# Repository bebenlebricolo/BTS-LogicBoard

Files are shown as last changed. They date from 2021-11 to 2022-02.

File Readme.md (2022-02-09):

# Index
- [BTS-LogicBoard](#bts-logicboard)
- [Features](#features)

# BTS-LogicBoard
Beer thermoregulation system logic board.
This board is meant to provide a PWM control signal to the [BTS-MainBoard-Control](https://github.com/bebenlebricolo/BTS-MainBoard-Control) board and will be driven by different input sources :
  1. External input mechanisms, implying and external trigger signal and a mechanical user interface such as switches and potentiometers.
  2. Temperature sensor(s) using thermistor based sensors

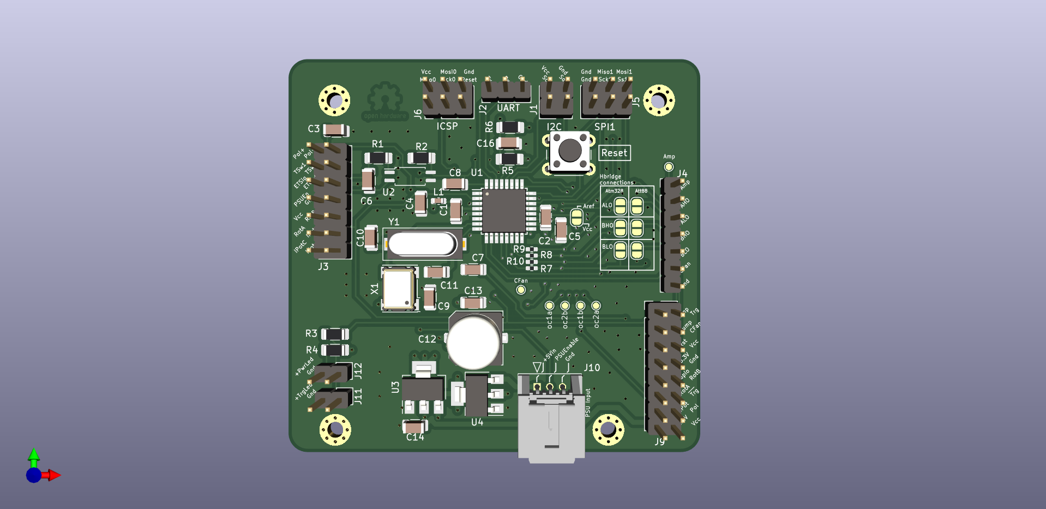
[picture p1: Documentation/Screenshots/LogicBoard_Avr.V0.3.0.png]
Screenshot V0.3.0

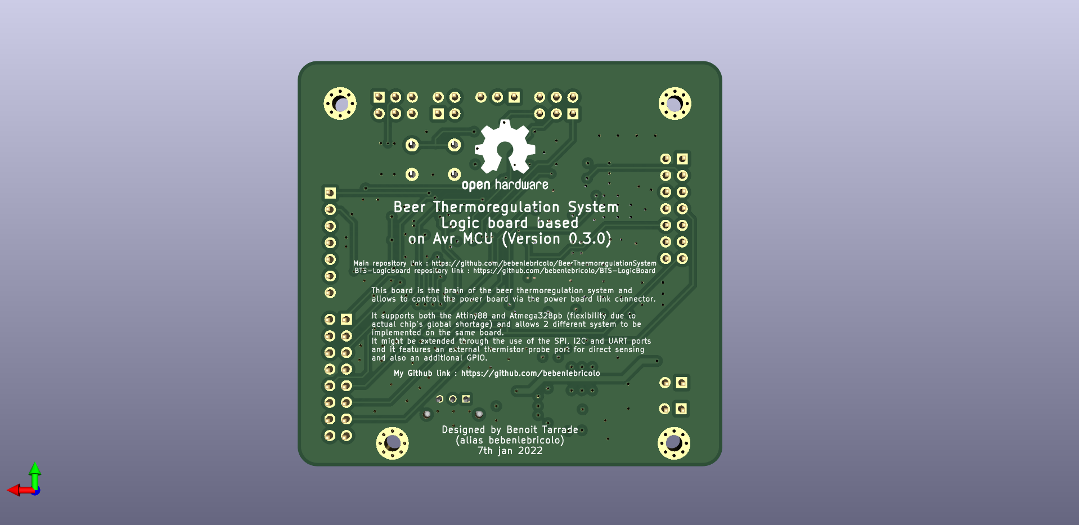
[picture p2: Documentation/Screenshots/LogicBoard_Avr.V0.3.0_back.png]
Screenshot V0.3.0


For more details on the current implementation, see [Notes of version 0.3.0](Notes/Notes_v0.3.0.md).

## 1. External triggering signal specificities
The later option was the first the be developped as it allowed to use an external regulation device as the triggering signal source (using a different power supply).
The input triggering signal is either *ON* or *OFF*.
As a consequence, we also need to get the "polarity" information, tells the system to warm up or cool down the thermal fluid.

## 2. Automatic temperature regulation using temperature sensors

This board is envisioned as a starting point as it only embeds generic electronic devices, meaning no code at all.
I've done this on purpose, to keep things relatively simple and eliminating the need to iterate over software revisions, bug fixes, etc.
As the functionalities implemented by this board are relatively simple, I thought it would be a nice alternative to go only with a NE555 (the famous one) and few other electronic components such as comparators and logic gates to perform the basic functions.

# Features
This boards boats the following features :
* 1 MHz (or so) PWM signal with linear (...or so) duty cycle control
* Cooling fan automatic turn on when board is enabled and turn off after a precalculated delay (around 120s) when the board is disabled
* Externaly driven : the PWM signal only starts up when an input signal is applied on the enable pins. This is meant to receive a pump driver signal in order to start up
* Mechanical interface (switches and potentiometer) with status leds
  * Power on status LED
  * PWM enabled status LED
  * PWM intensity status LED

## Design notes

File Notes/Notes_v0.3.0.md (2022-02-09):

- [Notes on board prototype version v0.3.0](#notes-on-board-prototype-version-v030)
- [Improvements from v0.2.0](#improvements-from-v020)
- [High speed PWM (1MHz +) using hardware timers and PWM](#high-speed-pwm-1mhz--using-hardware-timers-and-pwm)
- [Small issues](#small-issues)
  - [Hand soldering is quite challenging](#hand-soldering-is-quite-challenging)

# Notes on board prototype version v0.3.0
This board is built around 2 chips : either an Attiny88 or an Atmega328PB and accepts both. This choice of dual compatibility was made during the global chip shortage (2021/2022) and thus I had to find solutions to build the board with components I had at hands (Attiny88) in case the Atmega328PB were out of stock until late 2023.
As a result, as the Attiny88 is not as powerful and full featured as the Atmega328PB, some functionalities such as the UART and automatic HBridge free-wheeling won't be available ; and probably user interface will be leaner.

# Improvements from v0.2.0
* Switched to plain MCU design, noise sensitivity is reduced
* All important tracks were adjusted to be 50Ohms Z0 (characteristic impedance) in order to reduce signal reflection to a minimum
* Drive termination resistors were added on HBridge drive side (around 33 Ohms) to adapt for the ~20ish Ohms of Atmel chip's output characteristic impedance
* Tracks were optimized, as short and straight as possible, minimizing capacitive cross talk whenever possible (orthogonal track crossing as much as possible)
* Switching to 4 layers stackup design : signal (top), gnd, power, signal (bottom)
* Supports external triggering via the optocoupler
* Supports external triggering via signals headers for other extensions
* Provides Uart, Spi and I2C serial interfaces
  * The board could be extended with I2C screen, UART log channel, I2C/SPI additional temperature probes, etc..
* Extension friendly : user interface could be extended either using potentiometers, rotary encoders, switches in various configurations.

# High speed PWM (1MHz +) using hardware timers and PWM
Using hardware timers and PWM generation we can achieve 1MHz PWM with 1/12th (Attiny88) or 1/20th (Atmega328PB) resolution
We can also speed it up even more, sacrificing intermediate steps
This is required in order to take advantage of the high current inductors (10µH / 12A DC) which need to be run at very high frequencies in order to get the proper smoothing effect from them.

# Small issues
## Hand soldering is quite challenging
Hand soldering is quite challenging indeed because of the following points :
* Zones use direct and solid connection with all the pads ! -> soldering iron has to push a lot of heat before the solder starts to melt
  * Switch to thermal relief connection for all pads that don't require strong and stable GND/Power connections

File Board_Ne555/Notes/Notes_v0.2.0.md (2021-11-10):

- [Notes on board prototype version v0.2.0](#notes-on-board-prototype-version-v020)
- [Improvements from v0.1.0](#improvements-from-v010)
- [Fine(r) control over PWM duty cyle](#finer-control-over-pwm-duty-cyle)
- [Small issues](#small-issues)
  - [PWM controller speed is lower than the previous iteration, but this is an easyfix](#pwm-controller-speed-is-lower-than-the-previous-iteration-but-this-is-an-easyfix)
  - [Potentiometer wiring is reversed](#potentiometer-wiring-is-reversed)
  - [Output PWM goes up into the switch and goes down again on the board](#output-pwm-goes-up-into-the-switch-and-goes-down-again-on-the-board)
  - [When board is disabled (no input signal), output is still driven by the comparator](#when-board-is-disabled-no-input-signal-output-is-still-driven-by-the-comparator)

# Notes on board prototype version v0.2.0
This board prototype was called 'board-v1.1' earlier and I decided to rename it as v0.2.0 as semantically speaking, this board is also still a prototype (as the v0.1.0 was).
This board is built around a NE555 and fixes some important aspects of the first iteration.

# Improvements from v0.1.0
* Switched the NE555 PWM implementation to a fixed duty-cycle one and derive the PWM using a comparator
* Added hysteresis network resistors in comparators input circuitry
* Used CMOS NOT gates to handle input signal without impacting the other circuits
* Used an optoisolator to fully isolate the "external" circuitry from this one
* Remapped switches in order to have a more natural pin mapping
* Used a SPDT switch to enable / disable the circuit (PWM disable function is provided by the optoisolator circuitry).
* Added a status LED to indicate the PWM intensity
* Fine(r) control over PWM duty cycle
* Updated output connector wiring with a new inhibit pin (unused by this board, left for later use)

# Fine(r) control over PWM duty cyle
The PWM duty cycle control is done using the "pseudo sawtooth" signal taken from the NE555 load capacitor's charging/discharging cycles and comparing this signal with a constant voltage level, provided by the "Power control" potentiometer.
As its name states, the potentiometer effectively controls the output power of the system by varying the On time of the PWM ; the higher the duty cycle gets, the more power is requested.

However, the PWM control is far from perfect as the pseudo sawtooth signal is not a clean triangle wave and as such, the response is not really linear.
It is quite linear in the middle of the waveform, however the top and bottom edges are quite round and asymetrical.
As a result, it is really difficult to get a small duty cycle out the PWM controller and the generated PWM jumps almost directly from 0% to around 25/30%.
The same holds true for the high power side, although it is not as marked as the lower one.

# Small issues
## PWM controller speed is lower than the previous iteration, but this is an easyfix
The output PWM frequency is around 250kHz and is lower than the previous iteration (was between 400kHz - 750kHz).
This is mostly due to the fact that the NE555 circuit uses fairly high values for the resistors and capacitors to generate the signal and as such, this is an easy fix as we simply need to update those values to lower ones.

## Potentiometer wiring is reversed
The logic of the PWM comparator is reversed, this means that turning the knob to the right (the usual "more power" direction) actually decreases the duty cycle and vice-versa. This is an easy fix as well as we simply need to reverse the potentiometer wiring (connecting the + side to the left and - side to the right with the middle pin unchanged).

## Output PWM goes up into the switch and goes down again on the board
This has not shown to be an issue in itself while testing the board, however mechanically rerouting the PWM signal within the switch makes it go back and forth in non-isolated wires. If the wire length increases, it can easily pick up some ambient noise (acting as an antenna) and we might also observe signal reflection because we are expecting to be working around 1MHz.
A solution may consist in switching the signal using mosfet as unidirectional switches, without the signal leaving the board and making a loop.

## When board is disabled (no input signal), output is still driven by the comparator
I forgot to add an output protection layer that prevents the board from outputing a 100% duty cycle even when the NE555 is disabled.
This is due to the fact that the output stage is directly driven by the output comparator, and in some configurations lowering the potentiometer level low enough eratically triggers the comparator, which in turns generate a weird looking "PWM" signal (aperiodic). This stray output signal might cause some issues as it will trigger the power boards anyway, but without any cooling (fans are turned off in such a configuration).

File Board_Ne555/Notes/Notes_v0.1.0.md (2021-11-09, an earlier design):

- [Notes on board prototype version v0.1.0](#notes-on-board-prototype-version-v010)
- [Design flaws](#design-flaws)
  - [Comparators are messed up](#comparators-are-messed-up)
  - [PWM generator (NE555)](#pwm-generator-ne555)
  - [Switches are not mapped correctly](#switches-are-not-mapped-correctly)
  - [Input transistor network for the reset ability](#input-transistor-network-for-the-reset-ability)
  - [Input "pump on" signal is not isolated](#input-pump-on-signal-is-not-isolated)
  - [Fan triggering system does not really perform as expected](#fan-triggering-system-does-not-really-perform-as-expected)
  - [Enable/Disable switch implements the same feature twice](#enabledisable-switch-implements-the-same-feature-twice)
- [Proposed improvements](#proposed-improvements)
- [Bottomline](#bottomline)

# Notes on board prototype version v0.1.0
This board prototype was called 'board-v1' earlier and I decided to rename it as v0.1.0 as semantically speaking, this board was not ready yet.
This board was built around a NE555 and has several design flaws. It is **not** viable and burns as soon as we try to connect everything together.

# Design flaws
As said above, this board embeds quite a few errors :
## Comparators are messed up
* Both comparators had flipped 4 and 5 pins, as a result, there is some current rejection from Vdd through the input pins
* Both comparator are **not** 12V compatible : using 12V on VDD creates some magic smoke out of them (you learn the hard way... don't you ?)
* Both comparators [ONSemi's NCS2252](https://www.onsemi.com/pdf/datasheet/ncs2250-d.pdf) are in fact open drain and required extra output pullup resistor
* Comparators do not embed hysteresis resistor network, switch is quite sensitive and produces a fair amount of noise.

## PWM generator (NE555)
PWM generation is not stable, frequency varies with the potentiometer's input, which is not part of the "requirement".
Output signal is quite awful, we don't end up with a clean square wave

## Switches are not mapped correctly
Output pins on the board do not follow a natural pattern and is mapped like so :

| footprint | switch |
| --- | --- |
| 1 - 2 | 1 - 6  |
| 3 - 4 | 2 - 5  |
| 5 - 6 | 3 - 4  |

So it's really easy to mess up the wiring and end with something that really does not behave as expected.

## Input transistor network for the reset ability
Input transistor network fails to trigger the reset pin of the NE555 as the transistor in charge of this action saturates at 0.7V, which is still above the NE555's input threshold value for this pin. Next design implements a harder pull-down action using a saturated NPN with the collector-emitter voltage of 0.2V, which is plenty enough to turn off the NE555.

## Input "pump on" signal is not isolated
In the system that I'm using, the pump is driven by another system, on its own SMPS (Switching mode power supply).
As such, we don't really know about the ground connection of the other system and we can end with a floating gnd which is then connected to our system, potentially triggering some faults in the ATX power supply or worse, burning things down.
A solution would be to implement an optoisolated interface for the pump signal (aka start up signal). This is done in the next revision of this board.

## Fan triggering system does not really perform as expected
The fan triggering system was meant to provide a startup signal for the cooling fan driver, located on the BTS-MainBoard-Control board.
The main purpose of the input circuitry was to charge up a capacitor, then leaving it to discharge slowly for a preestablished time (around 120 seconds).
As I remember it, the overall system was not performing well and this was mostly due to the fact that input transistor network had some cross interferences between each transistors. I remedied this in the next revision with proper NOT gates and high speed comparators.

## Enable/Disable switch implements the same feature twice
The enable/Disable switch is used to turn the ATX power supply and enable the PWM signal at the same time.
We could simply rely on the pump activation in order to provide the same kind of functionality.

# Proposed improvements
* Switch the NE555 PWM implementation to a fixed duty-cycle one and derive the PWM using a comparator
* Add hysteresis network resistors in comparators input circuitry
* Use CMOS NOT gates to handle input signal without impacting the other circuits
* Use an optoisolator to fully isolate the "external" circuitry from this one
* Remap switches in order to have a more natural pin mapping
* Use a SPDT switch to enable / disable the circuit (PWM disable function is provided by the optoisolator circuitry).

# Bottomline
This board did provide some value as it clearly pointed out the design flaws of this iteration and gave me some good ideas on how to implement a new system.
However, I tried to fix this board with tiny wires, remapping pins and adding resistors ; however this whole new "flying" network made up for great antennas and completely defeated the purpose of having a "clean" PWM generation.

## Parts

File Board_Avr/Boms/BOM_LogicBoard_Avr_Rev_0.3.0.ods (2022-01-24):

Logic Board Avr revision 0.3.0 BOM sheet
Reference | Quantity | Value | Footprint | Datasheet
C1 C2 C6 C8 C9 C16 | 6 | 100nF | Capacitor_SMD:C_1206_3216Metric
C10 C11 | 2 | 10pF | Capacitor_SMD:C_1206_3216Metric
C12 | 1 | 470uF | Capacitor_SMD:C_Elec_8x6.2
C3 C4 C7 | 3 | 330nF | Capacitor_SMD:C_1206_3216Metric
C5 C13 C14 | 3 | 1uF | Capacitor_SMD:C_1206_3216Metric
H1 H2 H3 H4 | 4 | MountingHole_Pad | MountingHole:MountingHole_2.5mm_Pad_Via
J1 | 1 | I2C_Interface | Connector_PinHeader_2.54mm:PinHeader_2x02_P2.54mm_Vertical
J10 | 1 | PSU Connector | BTS-LogicBoard:559350310
J11 | 1 | TriggeredStatusLedConnector | Connector_PinHeader_2.54mm:PinHeader_1x02_P2.54mm_Vertical
J12 | 1 | PowerStatusLedConnector | Connector_PinHeader_2.54mm:PinHeader_1x02_P2.54mm_Vertical
J2 | 1 | UART_Interface | Connector_PinHeader_2.54mm:PinHeader_1x03_P2.54mm_Vertical
J3 | 1 | Mechanical user interface main connector | Connector_PinHeader_2.54mm:PinHeader_2x07_P2.54mm_Vertical
J4 | 1 | Power board connector | Connector_PinHeader_2.54mm:PinHeader_1x07_P2.54mm_Vertical
J5 | 1 | SPI Connector | Connector_PinHeader_2.54mm:PinHeader_2x03_P2.54mm_Vertical
J6 | 1 | ICSP Header | Connector_PinHeader_2.54mm:PinHeader_2x03_P2.54mm_Vertical
J9 | 1 | GPIO Connector | Connector_PinHeader_2.54mm:PinHeader_2x08_P2.54mm_Vertical
JP1 | 1 | Aref_jumper | Jumper:SolderJumper-2_P1.3mm_Open_RoundedPad1.0x1.5mm
JP2 | 1 | HB_ALO_AT88_JP | Jumper:SolderJumper-2_P1.3mm_Open_RoundedPad1.0x1.5mm
JP3 | 1 | HB_ALO_ATM328_JP | Jumper:SolderJumper-2_P1.3mm_Open_RoundedPad1.0x1.5mm
JP4 | 1 | HB_BHO_AT88_JP | Jumper:SolderJumper-2_P1.3mm_Open_RoundedPad1.0x1.5mm
JP5 | 1 | HB_BHO_ATM328_JP | Jumper:SolderJumper-2_P1.3mm_Open_RoundedPad1.0x1.5mm
JP6 | 1 | HB_BLO_AT88_JP | Jumper:SolderJumper-2_P1.3mm_Open_RoundedPad1.0x1.5mm
JP7 | 1 | HB_BLO_ATM328_JP | Jumper:SolderJumper-2_P1.3mm_Open_RoundedPad1.0x1.5mm
L1 | 1 | BLM18AG151SN1D | Capacitor_SMD:C_0603_1608Metric | https://docs.rs-online.com/b10d/0900766b811b5866.pdf
R1 R2 R3 R4 | 4 | 1k | Resistor_SMD:R_1206_3216Metric_Pad1.30x1.75mm_HandSolder
R5 | 1 | 10k | Resistor_SMD:R_1206_3216Metric_Pad1.30x1.75mm_HandSolder
R6 | 1 | 330 | Resistor_SMD:R_1206_3216Metric_Pad1.30x1.75mm_HandSolder
R7 R8 R9 R10 | 4 | 33 | Resistor_SMD:R_0402_1005Metric_Pad0.72x0.64mm_HandSolder
SW1 | 1 | Reset switch | Button_Switch_THT:SW_PUSH_6mm_H4.3mm
TP1 TP2 TP3 TP4 TP5 TP6 | 6 | TestPoint | TestPoint:TestPoint_Pad_D1.0mm
U1 | 1 | ATmega328PB-A | Package_QFP:TQFP-32_7x7mm_P0.8mm | http://ww1.microchip.com/downloads/en/DeviceDoc/40001906C.pdf
U2 | 1 | TLP291 | Package_SO:SOIC-4_4.55x2.6mm_P1.27mm | https://toshiba.semicon-storage.com/info/docget.jsp?did=12884&prodName=TLP291
U3 | 1 | NCP603SN330T1G | Package_SO:TSOP-5_1.65x3.05mm_P0.95mm | https://www.onsemi.com/pdf/datasheet/ncp603-d.pdf
U4 | 1 | LM1117-5.0 | Package_TO_SOT_SMD:SOT-223-3_TabPin2 | http://www.ti.com/lit/ds/symlink/lm1117.pdf
X1 | 1 | ASV-12.000MHZ-EJ-T | Oscillator:Oscillator_SMD_Abracon_ASV-4Pin_7.0x5.1mm | http://www.abracon.com/Oscillators/ASV.pdf
Y1 | 1 | ABLS-20.000MHz-16-A-4-H-T | BTS-LogicBoard:Crystal_SMD_TH_Combo_HC49-SD

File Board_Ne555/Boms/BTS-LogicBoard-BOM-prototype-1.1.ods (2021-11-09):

References | Quantity | Value | Unit price (€ ) As seen on RS | Price onboard | Component | Description | RS Part code | RS link | Vendor
C4 C13 | 2 | 1uF | 0,04 | 0,08 | GRM31MF51E475ZA01L | Unpolarized capacitor | 723-6629 | link (https://fr.rs-online.com/web/p/condensateurs-ceramique-multicouches/7236629/?sra=pmpn) | Murata
C5 C8 | 3 | 470uF | 0,35 | 1,05 | NAZT471M25V10X10.5LBF | Polarized capacitor | 742-3582 | link (https://fr.rs-online.com/web/p/condensateurs-electrolytiques/7423582) | NIC Components
C3 C9 C10 C11 C12 | 5 | 100nF | 0,113 | 0,565 | C3216JB2A104K | Unpolarized capacitor | 371-6714 | link (https://fr.rs-online.com/web/p/condensateurs-ceramique-multicouches/3716714/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) | TDK
C6, | 1 | 10nF | 0,181 | 0,181 | 223860115636 | Unpolarized capacitor | 669-8442 | link (https://fr.rs-online.com/web/p/condensateurs-ceramique-multicouches/6698442/) | Yageo
C7 (470pF instead) | 1 | 220pF | 0,026 | 0,026 | 12065A100JAT2A | Unpolarized capacitor | 136-4357 | link (https://fr.rs-online.com/web/p/condensateurs-ceramique-multicouches/1364357) | AVX
D1 D3 D4 | 3 | LED | 0,091 | 0,273 | L-132XGD | Light emitting diode | 860-9797 | link (https://fr.rs-online.com/web/p/led/8609797) | Kingbright
D2 | 1 | 1N4148W | 0,061 | 0,061 | 1N4148W | 75V 0.15A Fast Switching Diode, SOD-123 | 7003671P | link (https://fr.rs-online.com/web/p/diodes-de-commutation/7003671P/) | Vishay
H1, H2, H3, H4, | 4 | MountingHole_Pad | 0 | 0 | NA | Mounting Hole with connection | NA | NA | NA
J5 | 1 | Signal out connector (x6) | 0,461 | 0,461 | 505578-0671 | Molex MicroLock Plus connector (angled), 6 pins, 2Amps | 186-5197 | link (https://fr.rs-online.com/web/p/embases-circuits-imprimes/1865197) | Molex
J2, | 1 | Power connector (x3 pins) | 0,367 | 0,367 | 55935-0310 | Molex MicroClasp connector (angled), 3 pins, 3Amps | 188-024 | link (https://fr.rs-online.com/web/p/embases-circuits-imprimes/0188024) | Molex
J1 J4 | 2 | Switches connectors (03x02, + pins) | 0,217 | 0,434 | DF11-6DP-2DSA(08) | Hirose DF11 series, 6 pins, 2 rows, 2Amps | 605-6829 | link (https://fr.rs-online.com/web/p/embases-circuits-imprimes/6056829) | Hirose
J3, replaced by 2x1 header | 1 | Input pump on signal | 0,102 | 0,102 | 640454-2 | MTA-100, 2 pins 5.0A | 766-6604 | link (https://fr.rs-online.com/web/p/embases-circuits-imprimes/5355181) | TE-Connectivity
Q1 | 1 | BC817 | 0,173 | 0,173 | BC817-25LT3G | 0.8A Ic, 45V Vce, NPN Transistor, SOT-23 | 690-0076 | link (https://fr.rs-online.com/web/p/transistors-bipolaires/6900076/) | ON Semiconductor
R2 R4 R5 R13 R20 | 5 | 1k | 0,038 | 0,19 | CRG1206F1K0 | Resistor | 125-1190 | link (https://fr.rs-online.com/web/p/resistances-cms/1251190/) | TE-Connectivity
R14 R17 R18 | 3 | 56k | 0,074 | 0,222 | CRCW120656K0FKEA | Resistor | 679-223 | link (https://fr.rs-online.com/web/p/resistances-cms/6792231/) | Vishay
R1 R9 R12 R15 | 4 | 470 | 0,194 | 0,776 | CR1206-JW-471GLF | Resistor | 740-9120 | link (https://fr.rs-online.com/web/p/resistances-cms/7409120/) | Vishay
R19 (replaced by 5.6k) | 1 | 4.7k | 0,028 | 0,028 | CRG1206F4K7 | Resistor | 125-1191 | link (https://fr.rs-online.com/web/p/resistances-cms/1251191/) | TE-Connectivity
R7 R10 R11 | 3 | 10k | 0,029 | 0,087 | CRG1206F10K | Resistor | 125-1192 | link (https://fr.rs-online.com/web/p/resistances-cms/1251192/) | TE-Connectivity
R3 | 1 | 390k | 0,064 | 0,064 | CRCW1206390KFKEA | Resistor | 679-2073 | link (https://fr.rs-online.com/web/p/resistances-cms/6792073/) | Vishay
R6 | 1 | 220 | 0,11 | 0,11 | CRG1206F220R | Resistor | 223-2164 | link (https://fr.rs-online.com/web/p/resistances-cms/2232164/) | TE Connectivity
R8 R16 | 2 | 5.6k | 0,038 | 0,076 | CRG1206F5K6 | Resistor | 223-2366 | link (https://fr.rs-online.com/web/p/resistances-cms/2232366) | TE Connectivity
RV1, | 1 | R_POT | 0,82 | 0,82 | PTV09A-4225F-B103 | Potentiometer | 827-4990 | link (https://fr.rs-online.com/web/p/potentiometres/8274990/) | Bourns
SW1, SW2, | 2 | SW_DPDT_x2 | 3,35 | 6,7 | 2-1825138-8 | Switch, dual pole double throw, separate symbols | 710-9927 | link (https://fr.rs-online.com/web/p/interrupteurs-a-levier/7109927/) | TE-Connectivity
TP1 TP2 TP3 TP4 TP5 | 5 | TestPoints | 0 | 0 | NA | test point | NA | NA | NA
U1 U6 | 2 | NCS2252SN2T1G | 0,5 | 1 | NCS2252SN2T1G | Precisiong comparator, rail to rail (5V max) | 185-9083 | link (https://fr.rs-online.com/web/p/comparateurs/1859083/) | On Semiconductor
U4 | 1 | TLP291 | 0,14 | 0,14 | TLP291(Y,SE(T | Optocoupler / Optoisolator 80V | 896-2555 | link (https://fr.rs-online.com/web/p/optocoupleurs/8962555) | Toshiba
U3 U5 | 2 | 74HC1GU04 | 0,04 | 0,08 | 74HC1GU04GW-Q100,1 | Not gate (CMOS inverter) | 152-6496 | link (https://fr.rs-online.com/web/p/inverseurs/1526496/) | Nexperia
U8 | 1 | LM1117IMP-5,0 | 1,334 | 1,334 | LM1117IMP-5.0/NOPB | 5V LDO regulator, SOT-223 | 535-8641 | link (https://fr.rs-online.com/web/p/regulateurs-de-tension/5358641/) | Texas Instruments
U2, | 1 | NE555D/TS555 | 0,359 | 0,359 | NE555DR | Precision Timers, 555 compatible, SOIC-8 | 197-7393 | link (https://fr.rs-online.com/web/p/timers/1977393/) | Texas Instruments
Total component price (€)
15,759
Optional
Description | Reference | Manufacturer | Part number | Unit price
Wire to board Connector | MTA-100 | TE-Connectivity | 3-640441-2 | 0,271 | 543-7700 | link (https://fr.rs-online.com/web/p/connecteurs-idc/5437700)
 | 2 wires

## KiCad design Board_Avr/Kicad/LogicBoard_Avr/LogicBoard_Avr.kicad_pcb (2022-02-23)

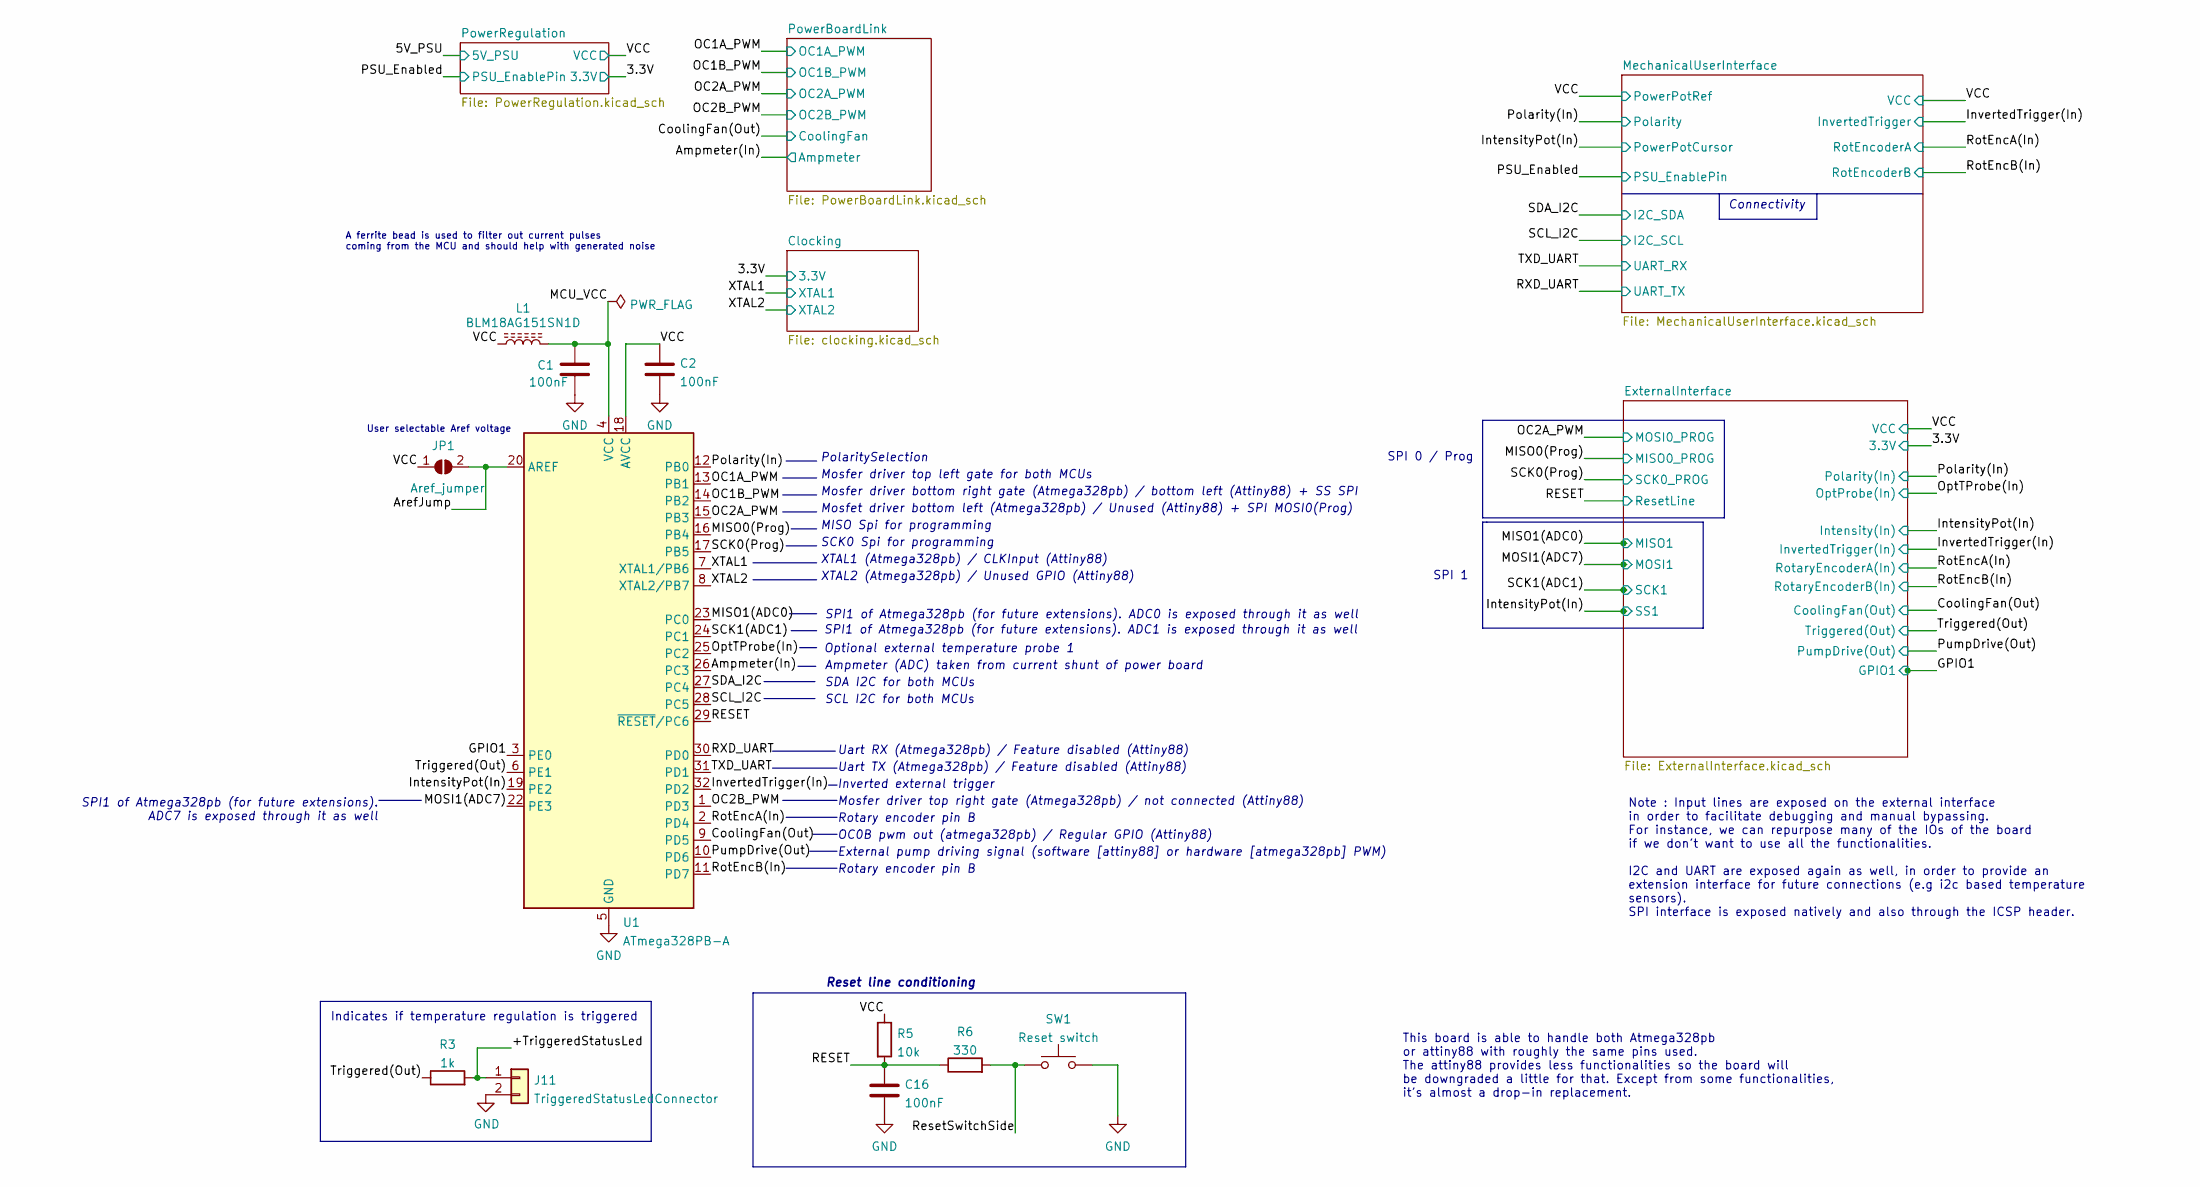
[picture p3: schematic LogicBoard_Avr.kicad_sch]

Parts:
C1, C2, C16: 100nF; C_1206_3216Metric
J11: TriggeredStatusLedConnector; PinHeader_1x02_P2.54mm_Vertical
JP1: Aref_jumper; SolderJumper-2_P1.3mm_Open_RoundedPad1.0x1.5mm
L1: BLM18AG151SN1D; L_0603_1608Metric
R3: 1k; R_1206_3216Metric_Pad1.30x1.75mm_HandSolder
R5: 10k; R_1206_3216Metric_Pad1.30x1.75mm_HandSolder
R6: 330; R_1206_3216Metric_Pad1.30x1.75mm_HandSolder
SW1: Reset switch; SW_PUSH_6mm_H4.3mm
U1: ATmega328PB-A; TQFP-32_7x7mm_P0.8mm

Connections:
/+TriggeredStatusLed: J11.1, R3.2
/Ampmeter(In): U1.26 (PC3); also elsewhere on the board
/ArefJump: JP1.2 (B), U1.20 (AREF)
/CoolingFan(Out): U1.9 (PD5); also elsewhere on the board
/GPIO1: U1.3 (PE0); also elsewhere on the board
/IntensityPot(In): U1.19 (PE2); also elsewhere on the board
/InvertedTrigger(In): U1.32 (PD2); also elsewhere on the board
/MCU_VCC: C1.1, L1.2, U1.4 (VCC)
/MISO0(Prog): U1.16 (PB4); also elsewhere on the board
/MISO1(ADC0): U1.23 (PC0); also elsewhere on the board
/MOSI1(ADC7): U1.22 (PE3); also elsewhere on the board
/OC1A_PWM: U1.13 (PB1); also elsewhere on the board
/OC1B_PWM: U1.14 (PB2); also elsewhere on the board
/OC2A_PWM: U1.15 (PB3); also elsewhere on the board
/OC2B_PWM: U1.1 (PD3); also elsewhere on the board
/OptTProbe(In): U1.25 (PC2); also elsewhere on the board
/Polarity(In): U1.12 (PB0); also elsewhere on the board
/PumpDrive(Out): U1.10 (PD6); also elsewhere on the board
/RESET: C16.1, R5.2, R6.1, U1.29 (~RESET/PC6); also elsewhere on the board
/RXD_UART: U1.30 (PD0); also elsewhere on the board
/ResetSwitchSide: R6.2, SW1.1
/RotEncA(In): U1.2 (PD4); also elsewhere on the board
/RotEncB(In): U1.11 (PD7); also elsewhere on the board
/SCK0(Prog): U1.17 (PB5); also elsewhere on the board
/SCK1(ADC1): U1.24 (PC1); also elsewhere on the board
/SCL_I2C: U1.28 (PC5); also elsewhere on the board
/SDA_I2C: U1.27 (PC4); also elsewhere on the board
/TXD_UART: U1.31 (PD1); also elsewhere on the board
/Triggered(Out): R3.1, U1.6 (PE1); also elsewhere on the board
/VCC: C2.1, JP1.1 (A), L1.1, R5.1, U1.18 (AVCC); also elsewhere on the board
/XTAL1: U1.7 (XTAL1/PB6); also elsewhere on the board
/XTAL2: U1.8 (XTAL2/PB7)
GND: C1.2, C2.2, C16.2, J11.2, SW1.2, U1.5 (GND), U1.21 (GND); also elsewhere on the board

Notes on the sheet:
SPI1 of Atmega328pb (for future extensions). ADC7 is exposed through it as well
Rotary encoder pin B
PolaritySelection
User selectable Aref voltage
OC0B pwm out (atmega328pb) / Regular GPIO (Attiny88)
Note : Input lines are exposed on the external interface in order to facilitate debugging and manual bypassing. For instance, we can repurpose many of the IOs of the board if we don't want to use all the functionalities. I2C and UART are exposed again as well, in order to provide an extension inter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
SPI 1
SPI1 of Atmega328pb (for future extensions). ADC1 is exposed through it as well
This board is able to handle both Atmega328pb or attiny88 with roughly the same pins used. The attiny88 provides less functionalities so the board will be downgraded a little for that. Except from some functionalities, it's almost a drop-in replacement.
XTAL2 (Atmega328pb) / Unused GPIO (Attiny88)
Mosfet driver bottom left (Atmega328pb) / Unused (Attiny88) + SPI MOSI0(Prog)
Reset line conditioning
SPI1 of Atmega328pb (for future extensions). ADC0 is exposed through it as well
Inverted external trigger
Connectivity
SDA I2C for both MCUs
MISO Spi for programming
External pump driving signal (software [attiny88] or hardware [atmega328pb] PWM)
Uart TX (Atmega328pb) / Feature disabled (Attiny88)
Mosfer driver bottom right gate (Atmega328pb) / bottom left (Attiny88) + SS SPI
Mosfer driver top left gate for both MCUs
Mosfer driver top right gate (Atmega328pb) / not connected (Attiny88)
XTAL1 (Atmega328pb) / CLKInput (Attiny88)
Ampmeter (ADC) taken from current shunt of power board
SCK0 Spi for programming
Optional external temperature probe 1
Indicates if temperature regulation is triggered
SPI 0 / Prog
Uart RX (Atmega328pb) / Feature disabled (Attiny88)
SCL I2C for both MCUs
A ferrite bead is used to filter out current pulses coming from the MCU and should help with generated noise

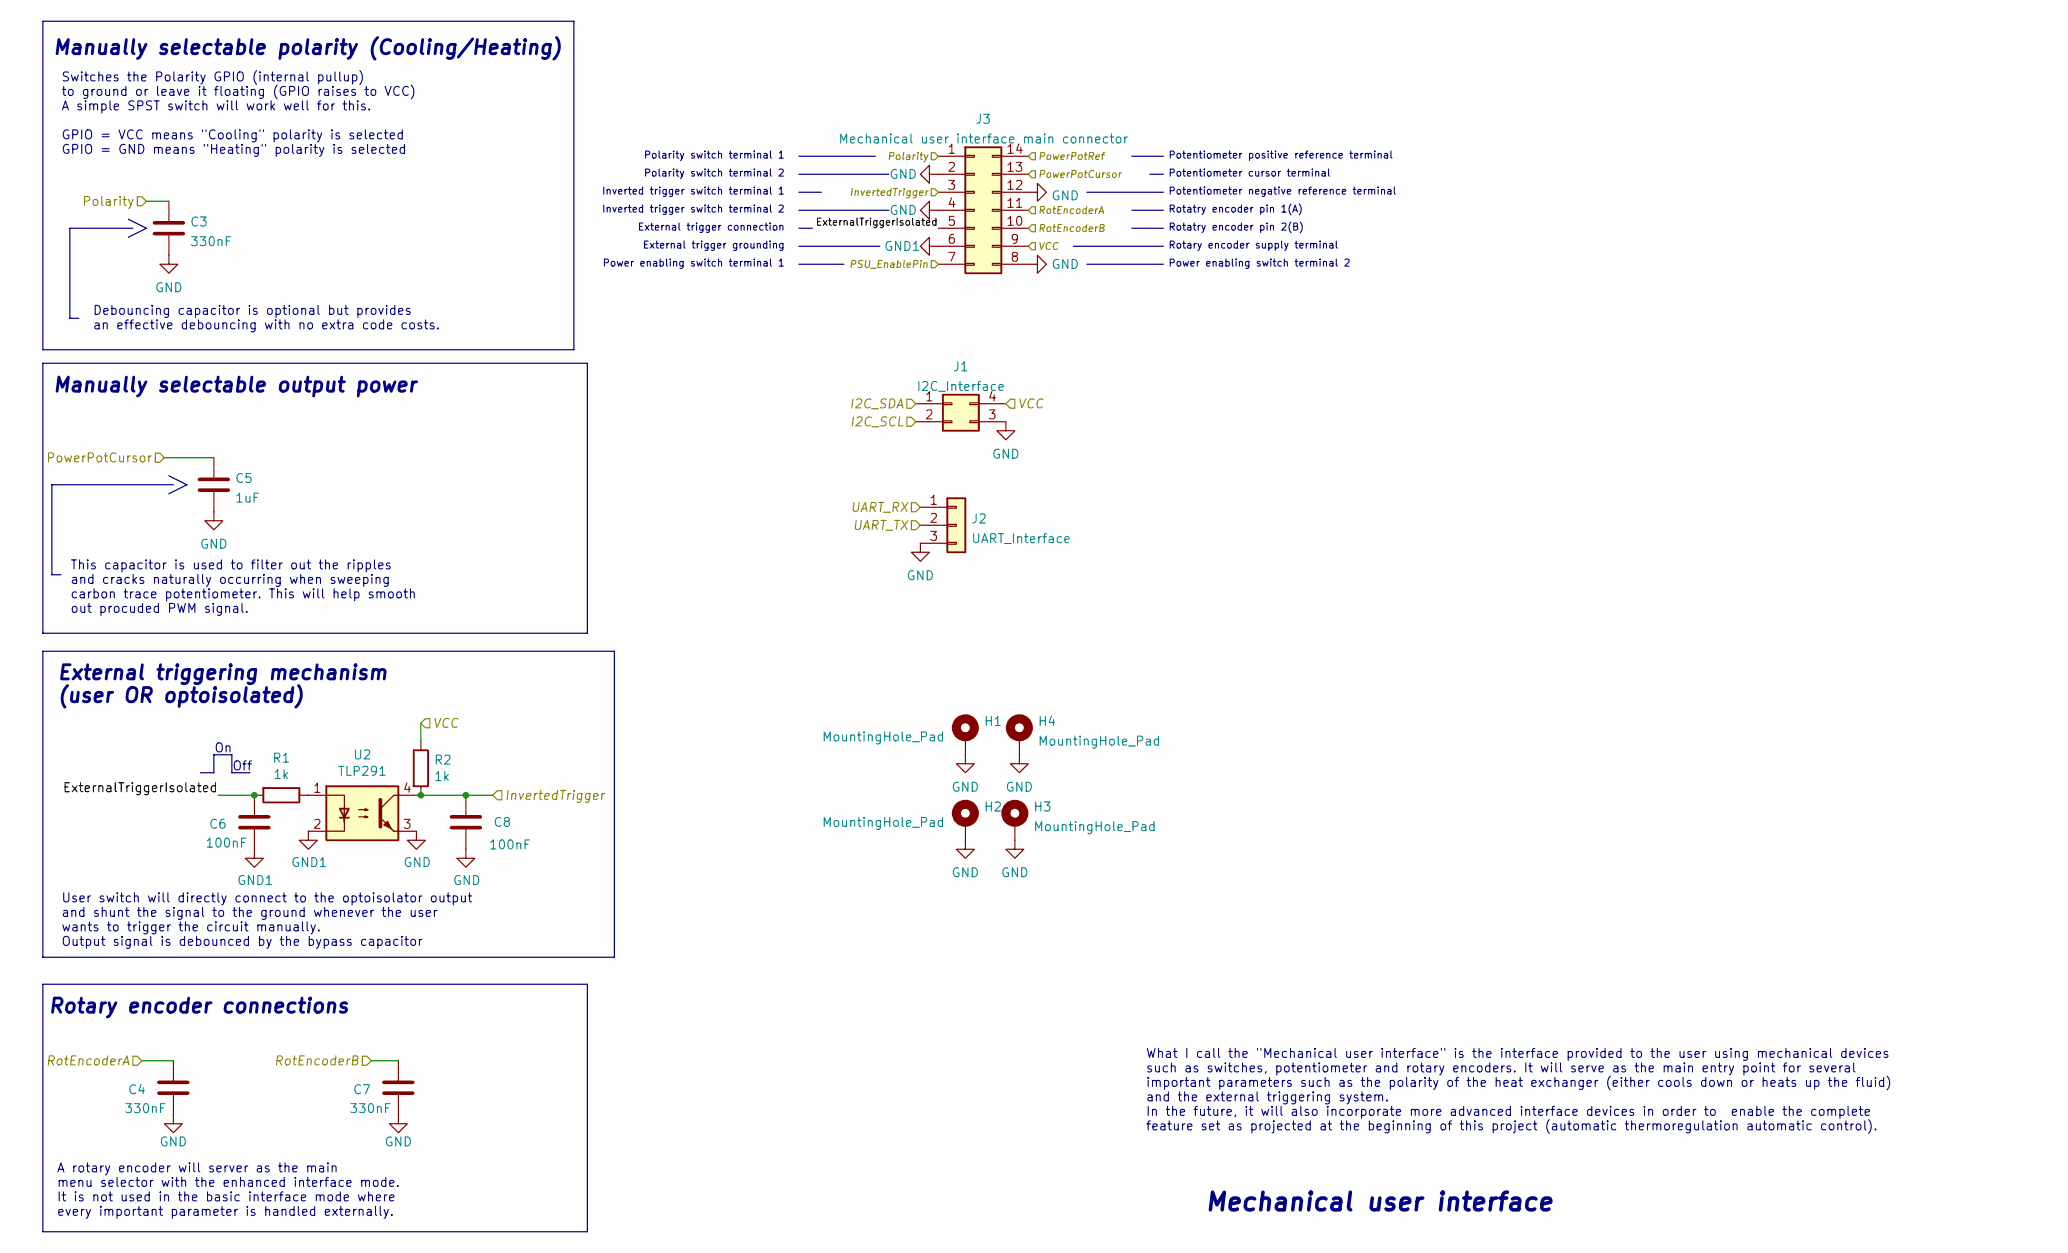
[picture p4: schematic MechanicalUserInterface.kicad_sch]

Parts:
C3, C4, C7: 330nF; C_1206_3216Metric
C5: 1uF; C_1206_3216Metric
C6, C8: 100nF; C_1206_3216Metric
H1, H2, H3, H4: MountingHole_Pad; MountingHole_2.5mm_Pad_Via
J1: I2C_Interface; PinHeader_2x02_P2.54mm_Vertical
J2: UART_Interface; PinHeader_1x03_P2.54mm_Vertical
J3: Mechanical user interface main connector; PinHeader_2x07_P2.54mm_Vertical
R1, R2: 1k; R_1206_3216Metric_Pad1.30x1.75mm_HandSolder
U2: TLP291; SOIC-4_4.55x2.6mm_P1.27mm

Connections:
/IntensityPot(In): C5.1, J3.13; also elsewhere on the board
/InvertedTrigger(In): C8.2, J3.3, R2.2, U2.4; also elsewhere on the board
/MechanicalUserInterface/ExternalTriggerIsolated: C6.2, J3.5, R1.2
/PSU_Enabled: J3.7; also elsewhere on the board
/Polarity(In): C3.1, J3.1; also elsewhere on the board
/RXD_UART: J2.2; also elsewhere on the board
/RotEncA(In): C4.2, J3.11; also elsewhere on the board
/RotEncB(In): C7.2, J3.10; also elsewhere on the board
/SCL_I2C: J1.2; also elsewhere on the board
/SDA_I2C: J1.1; also elsewhere on the board
/TXD_UART: J2.1; also elsewhere on the board
/VCC: J1.4, J3.9, J3.14, R2.1; also elsewhere on the board
GND: C3.2, C4.1, C5.2, C7.1, C8.1, H1.1, H2.1, H3.1, H4.1, J1.3, J2.3, J3.2, J3.4, J3.8, J3.12, U2.3; also elsewhere on the board
GND1: C6.1, J3.6, U2.2
unnamed: R1.1, U2.1

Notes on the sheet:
Rotatry encoder pin 2(B)
Rotatry encoder pin 1(A)
External triggering mechanism (user OR optoisolated)
A rotary encoder will server as the main menu selector with the enhanced interface mode. It is not used in the basic interface mode where every important parameter is handled externally.
Manually selectable polarity (Cooling/Heating)
Inverted trigger switch terminal 1
Polarity switch terminal 2
What I call the "Mechanical user interface" is the interface provided to the user using mechanical devices such as switches, potentiometer and rotary encoders. It will serve as the main entry point for several important parameters such as the polarity of the heat exchanger (either cools down or hea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
Debouncing capacitor is optional but provides an effective debouncing with no extra code costs.
External trigger grounding
Polarity switch terminal 1
Manually selectable output power
Off
User switch will directly connect to the optoisolator output and shunt the signal to the ground whenever the user wants to trigger the circuit manually. Output signal is debounced by the bypass capacitor
Switches the Polarity GPIO (internal pullup) to ground or leave it floating (GPIO raises to VCC) A simple SPST switch will work well for this. GPIO = VCC means "Cooling" polarity is selected GPIO = GND means "Heating" polarity is selected
Potentiometer cursor terminal
Potentiometer positive reference terminal
Potentiometer negative reference terminal
Mechanical user interface
Power enabling switch terminal 1
External trigger connection
Inverted trigger switch terminal 2
Rotary encoder supply terminal
This capacitor is used to filter out the ripples and cracks naturally occurring when sweeping carbon trace potentiometer. This will help smooth out procuded PWM signal.
Rotary encoder connections
Power enabling switch terminal 2

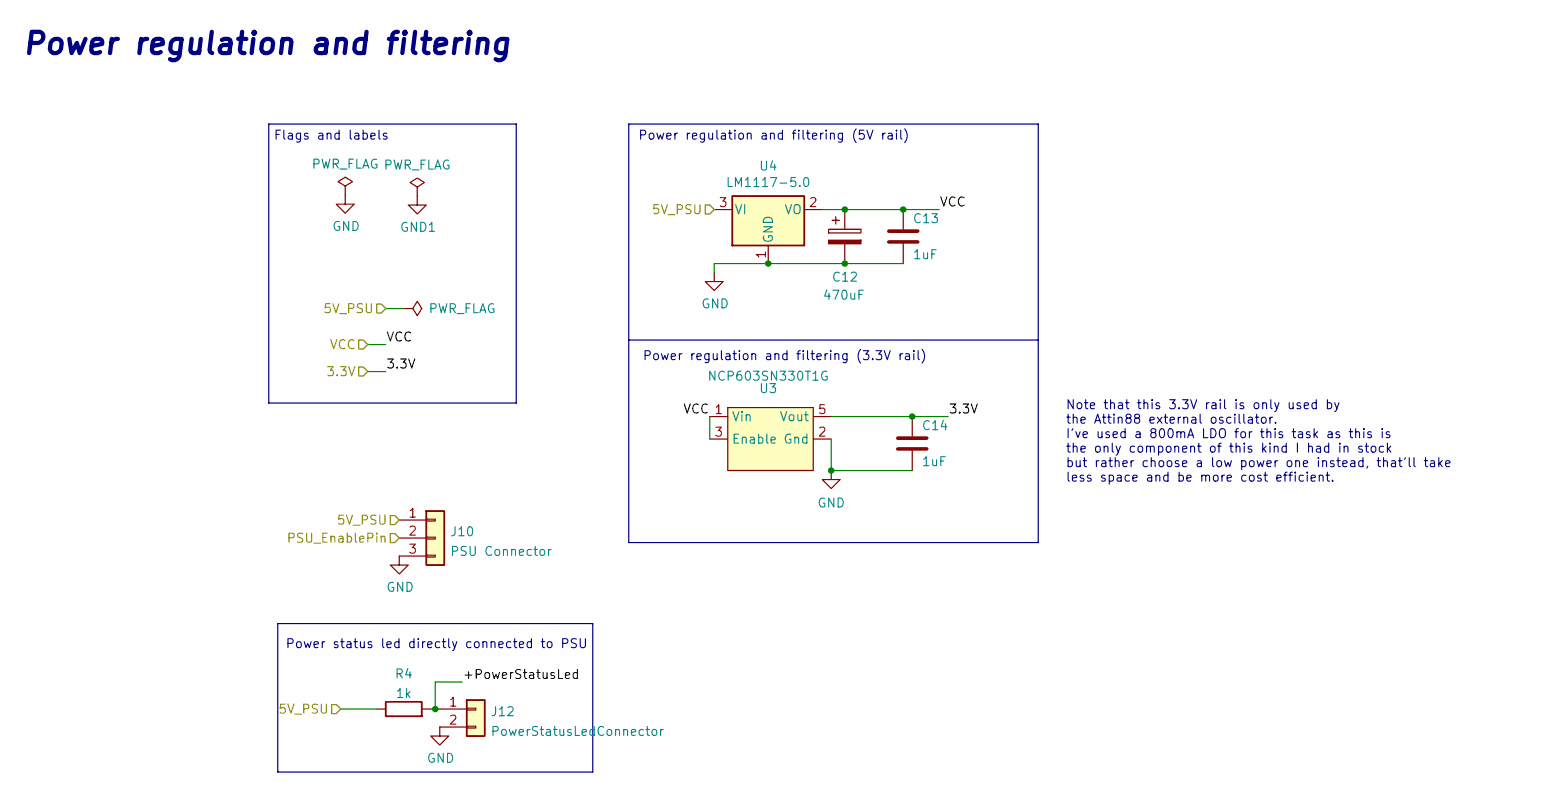
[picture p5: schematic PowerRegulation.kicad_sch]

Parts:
C12: 470uF; C_Elec_8x6.2
C13, C14: 1uF; C_1206_3216Metric
J10: PSU Connector; 559350310
J12: PowerStatusLedConnector; PinHeader_1x02_P2.54mm_Vertical
R4: 1k; R_1206_3216Metric_Pad1.30x1.75mm_HandSolder
U3: NCP603SN330T1G; TSOP-5_1.65x3.05mm_P0.95mm
U4: LM1117-5.0; SOT-223-3_TabPin2

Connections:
/3.3V: C14.1, U3.5 (Vout); also elsewhere on the board
/5V_PSU: J10.1, R4.1, U4.3 (VI)
/PSU_Enabled: J10.2; also elsewhere on the board
/PowerRegulation/+PowerStatusLed: J12.1, R4.2
/VCC: C12.1, C13.1, U3.1 (Vin), U3.3 (Enable), U4.2 (VO); also elsewhere on the board
GND: C12.2, C13.2, C14.2, J10.3, J12.2, U3.2 (Gnd), U4.1 (GND); also elsewhere on the board

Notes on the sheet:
Note that this 3.3V rail is only used by the Attin88 external oscillator. I've used a 800mA LDO for this task as this is the only component of this kind I had in stock but rather choose a low power one instead, that'll take less space and be more cost efficient.
Power regulation and filtering (5V rail)
Power regulation and filtering (3.3V rail)
Power status led directly connected to PSU
Power regulation and filtering
Flags and labels

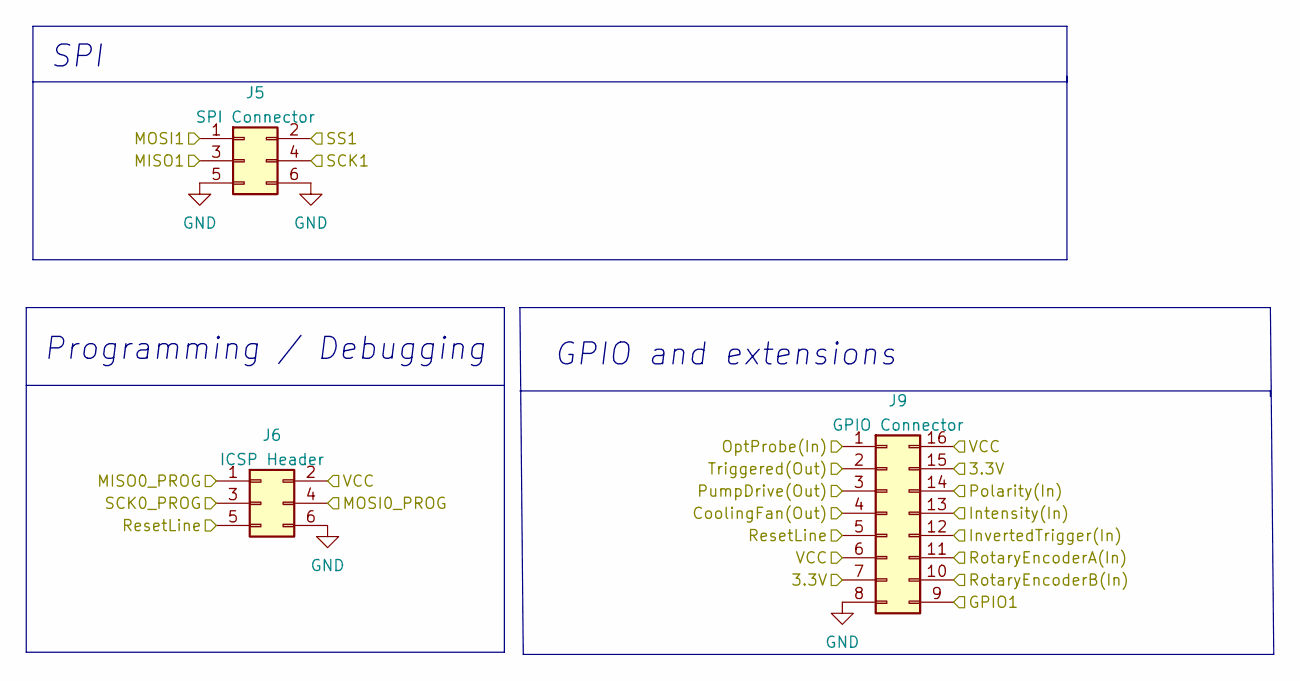
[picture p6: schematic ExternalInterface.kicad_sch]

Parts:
J5: SPI Connector; PinHeader_2x03_P2.54mm_Vertical
J6: ICSP Header; PinHeader_2x03_P2.54mm_Vertical
J9: GPIO Connector; PinHeader_2x08_P2.54mm_Vertical

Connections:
/3.3V: J9.7, J9.15; also elsewhere on the board
/CoolingFan(Out): J9.4; also elsewhere on the board
/GPIO1: J9.9; also elsewhere on the board
/IntensityPot(In): J5.2, J9.13; also elsewhere on the board
/InvertedTrigger(In): J9.12; also elsewhere on the board
/MISO0(Prog): J6.1; also elsewhere on the board
/MISO1(ADC0): J5.3; also elsewhere on the board
/MOSI1(ADC7): J5.1; also elsewhere on the board
/OC2A_PWM: J6.4; also elsewhere on the board
/OptTProbe(In): J9.1; also elsewhere on the board
/Polarity(In): J9.14; also elsewhere on the board
/PumpDrive(Out): J9.3; also elsewhere on the board
/RESET: J6.5, J9.5; also elsewhere on the board
/RotEncA(In): J9.11; also elsewhere on the board
/RotEncB(In): J9.10; also elsewhere on the board
/SCK0(Prog): J6.3; also elsewhere on the board
/SCK1(ADC1): J5.4; also elsewhere on the board
/Triggered(Out): J9.2; also elsewhere on the board
/VCC: J6.2, J9.6, J9.16; also elsewhere on the board
GND: J5.5, J5.6, J6.6, J9.8; also elsewhere on the board

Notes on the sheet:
GPIO and extensions
SPI
Programming / Debugging

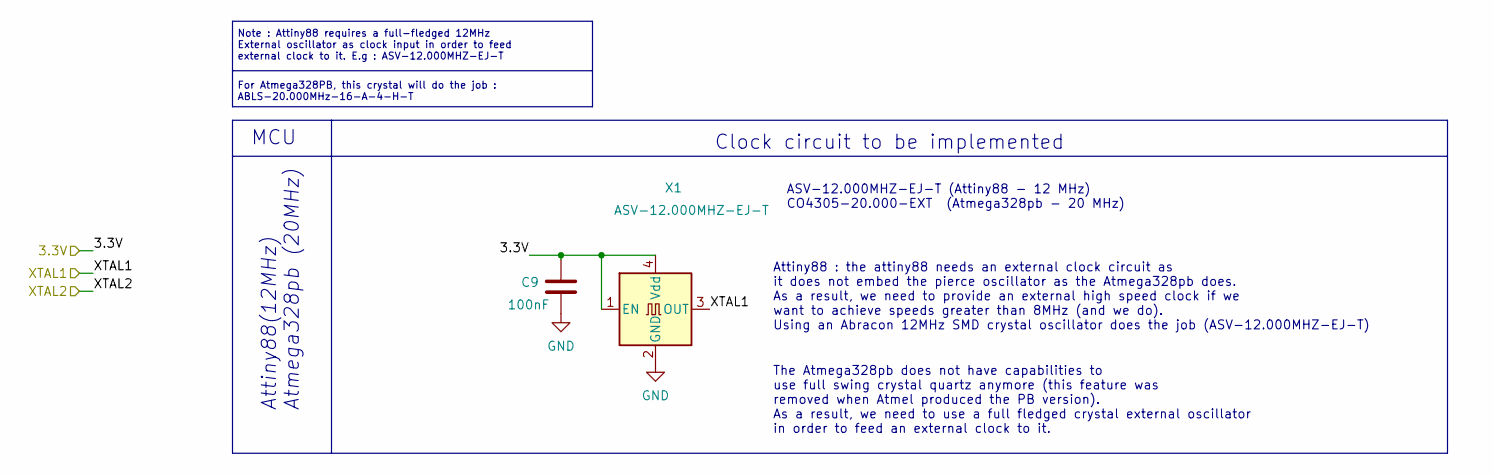
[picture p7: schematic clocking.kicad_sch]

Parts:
C9: 100nF; C_1206_3216Metric
X1: ASV-12.000MHZ-EJ-T; Oscillator_SMD_Abracon_ASV-4Pin_7.0x5.1mm

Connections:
/3.3V: C9.1, X1.1 (EN), X1.4 (Vdd); also elsewhere on the board
/XTAL1: X1.3 (OUT); also elsewhere on the board
GND: C9.2, X1.2 (GND); also elsewhere on the board

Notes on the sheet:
Attiny88(12MHz) Atmega328pb (20MHz)
For Atmega328PB, this crystal will do the job : ABLS-20.000MHz-16-A-4-H-T
Attiny88 : the attiny88 needs an external clock circuit as it does not embed the pierce oscillator as the Atmega328pb does. As a result, we need to provide an external high speed clock if we want to achieve speeds greater than 8MHz (and we do). Using an Abracon 12MHz SMD crystal oscillator does the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
MCU
ASV-12.000MHZ-EJ-T (Attiny88 - 12 MHz) CO4305-20.000-EXT (Atmega328pb - 20 MHz)
Clock circuit to be implemented
Note : Attiny88 requires a full-fledged 12MHz External oscillator as clock input in order to feed external clock to it. E.g : ASV-12.000MHZ-EJ-T
The Atmega328pb does not have capabilities to use full swing crystal quartz anymore (this feature was removed when Atmel produced the PB version). As a result, we need to use a full fledged crystal external oscillator in order to feed an external clock to it.

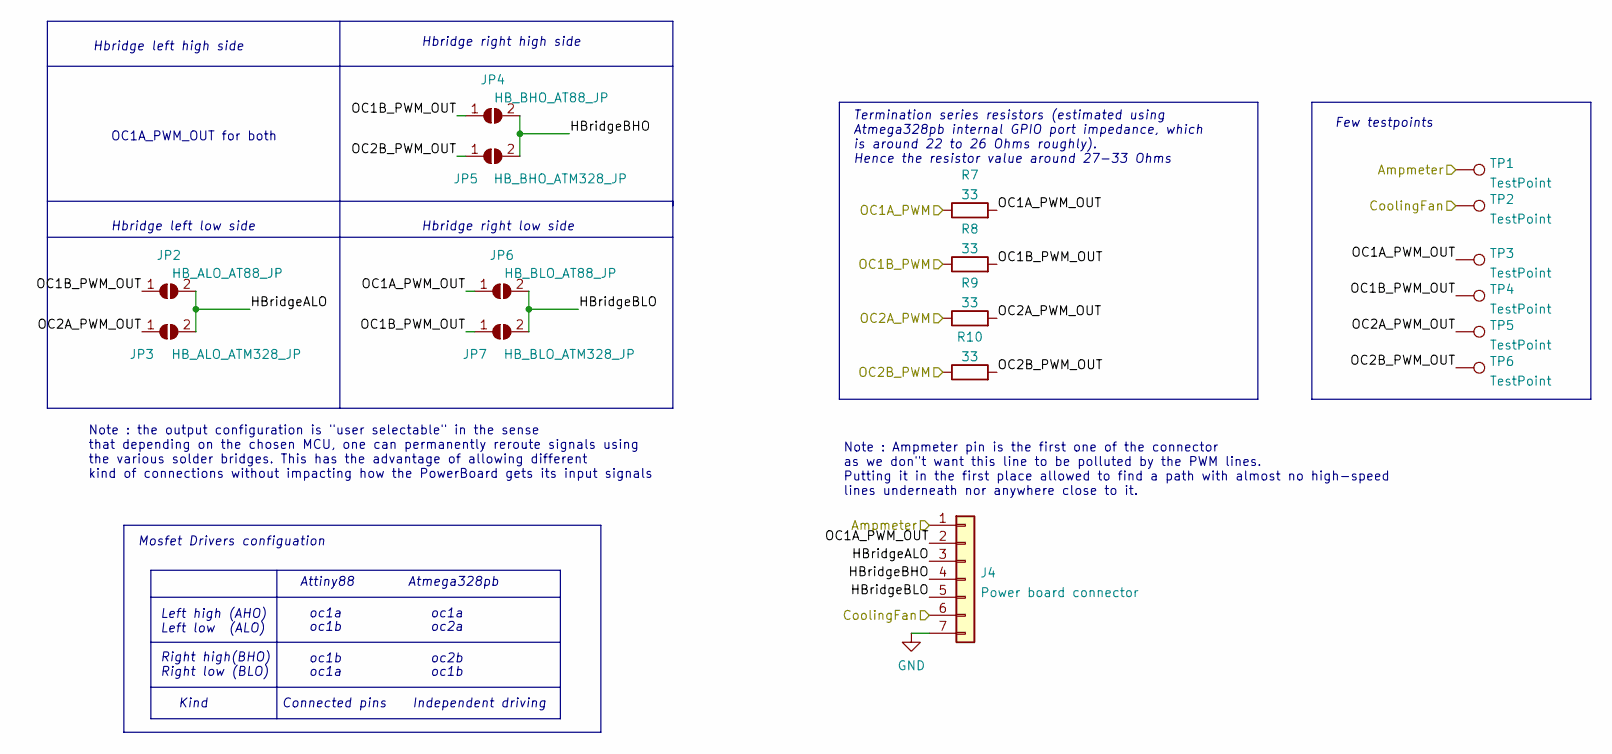
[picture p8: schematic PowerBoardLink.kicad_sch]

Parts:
J4: Power board connector; PinHeader_1x07_P2.54mm_Vertical
JP2: HB_ALO_AT88_JP; SolderJumper-2_P1.3mm_Open_RoundedPad1.0x1.5mm
JP3: HB_ALO_ATM328_JP; SolderJumper-2_P1.3mm_Open_RoundedPad1.0x1.5mm
JP4: HB_BHO_AT88_JP; SolderJumper-2_P1.3mm_Open_RoundedPad1.0x1.5mm
JP5: HB_BHO_ATM328_JP; SolderJumper-2_P1.3mm_Open_RoundedPad1.0x1.5mm
JP6: HB_BLO_AT88_JP; SolderJumper-2_P1.3mm_Open_RoundedPad1.0x1.5mm
JP7: HB_BLO_ATM328_JP; SolderJumper-2_P1.3mm_Open_RoundedPad1.0x1.5mm
R7, R8, R9, R10: 33; R_0402_1005Metric_Pad0.72x0.64mm_HandSolder
TP1, TP2, TP3, TP4, TP5, TP6: TestPoint; TestPoint_Pad_D1.0mm

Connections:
/Ampmeter(In): J4.1, TP1.1; also elsewhere on the board
/CoolingFan(Out): J4.6, TP2.1; also elsewhere on the board
/OC1A_PWM: R7.1; also elsewhere on the board
/OC1B_PWM: R8.1; also elsewhere on the board
/OC2A_PWM: R9.1; also elsewhere on the board
/OC2B_PWM: R10.1; also elsewhere on the board
/PowerBoardLink/HBridgeALO: J4.3, JP2.2 (B), JP3.2 (B)
/PowerBoardLink/HBridgeBHO: J4.4, JP4.2 (B), JP5.2 (B)
/PowerBoardLink/HBridgeBLO: J4.5, JP6.2 (B), JP7.2 (B)
/PowerBoardLink/OC1A_PWM_OUT: J4.2, JP6.1 (A), R7.2, TP3.1
/PowerBoardLink/OC1B_PWM_OUT: JP2.1 (A), JP4.1 (A), JP7.1 (A), R8.2, TP4.1
/PowerBoardLink/OC2A_PWM_OUT: JP3.1 (A), R9.2, TP5.1
/PowerBoardLink/OC2B_PWM_OUT: JP5.1 (A), R10.2, TP6.1
GND: J4.7; also elsewhere on the board

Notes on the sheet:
Note : the output configuration is "user selectable" in the sense that depending on the chosen MCU, one can permanently reroute signals using the various solder bridges. This has the advantage of allowing different kind of connections without impacting how the PowerBoard gets its input signals
Kind
Connected pins
Hbridge right high side
Hbridge right low side
Hbridge left high side
Mosfet Drivers configuation
Left high (AHO) Left low (ALO) Right high(BHO) Right low (BLO)
oc2a
Few testpoints
oc1b
Atmega328pb
Note : Ampmeter pin is the first one of the connector as we don"t want this line to be polluted by the PWM lines. Putting it in the first place allowed to find a path with almost no high-speed lines underneath nor anywhere close to it.
Termination series resistors (estimated using Atmega328pb internal GPIO port impedance, which is around 22 to 26 Ohms roughly). Hence the resistor value around 27-33 Ohms
oc1a
Attiny88
Independent driving
OC1A_PWM_OUT for both
oc2b
Hbridge left low side

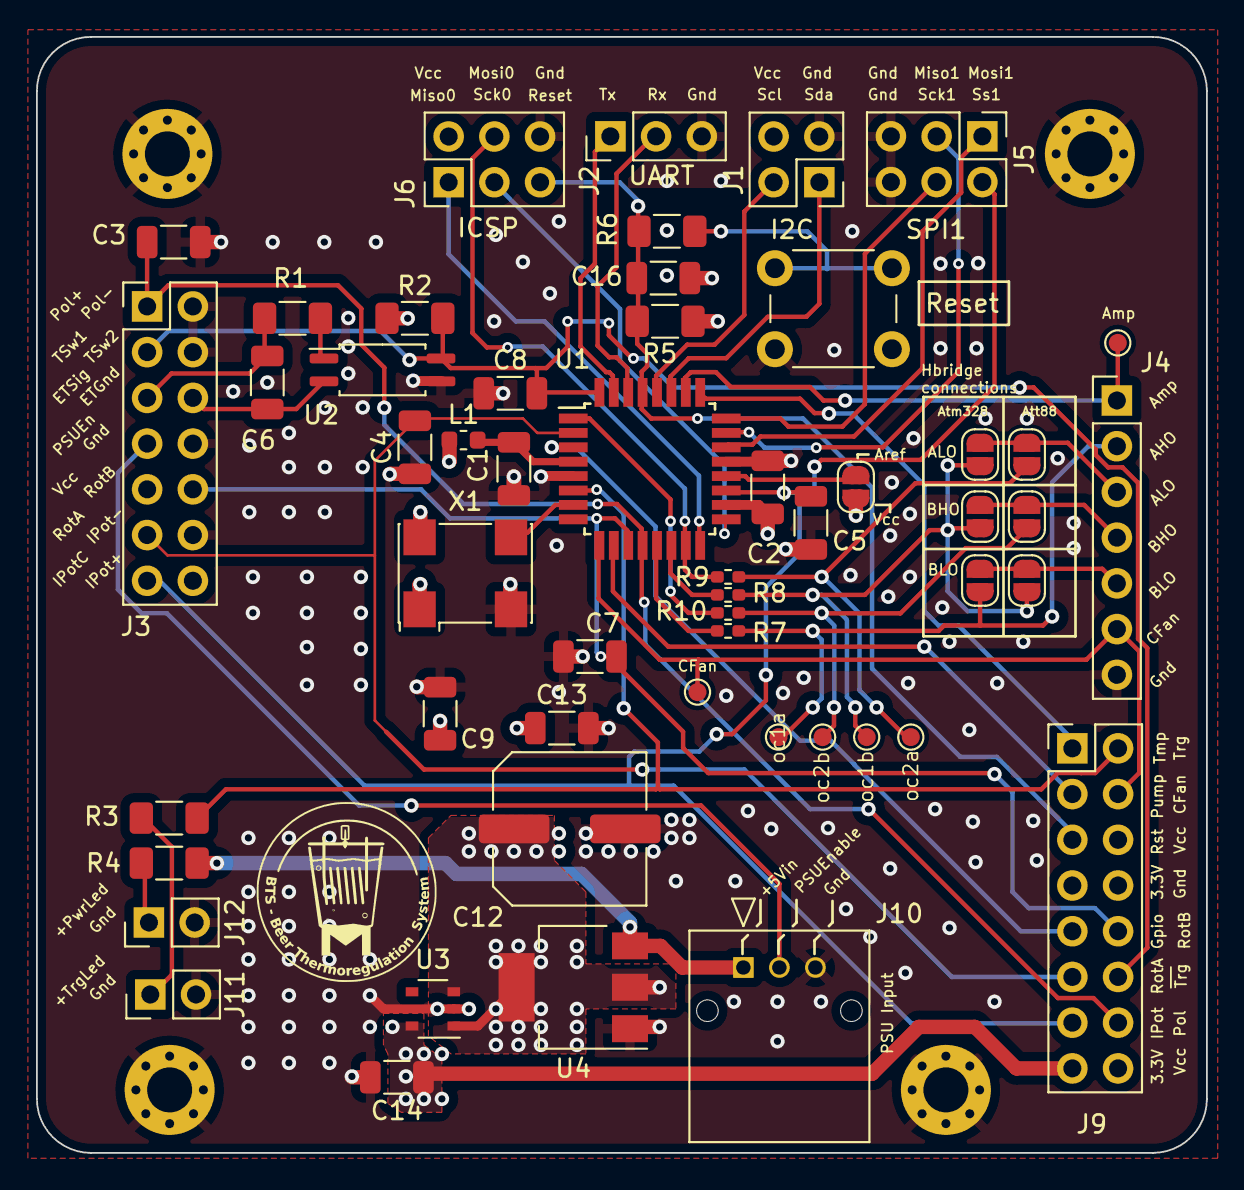
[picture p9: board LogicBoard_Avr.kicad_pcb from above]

Board: 4 copper layers, 65.0 x 62.0 mm, 57 parts (0 on the bottom side), 46 nets.

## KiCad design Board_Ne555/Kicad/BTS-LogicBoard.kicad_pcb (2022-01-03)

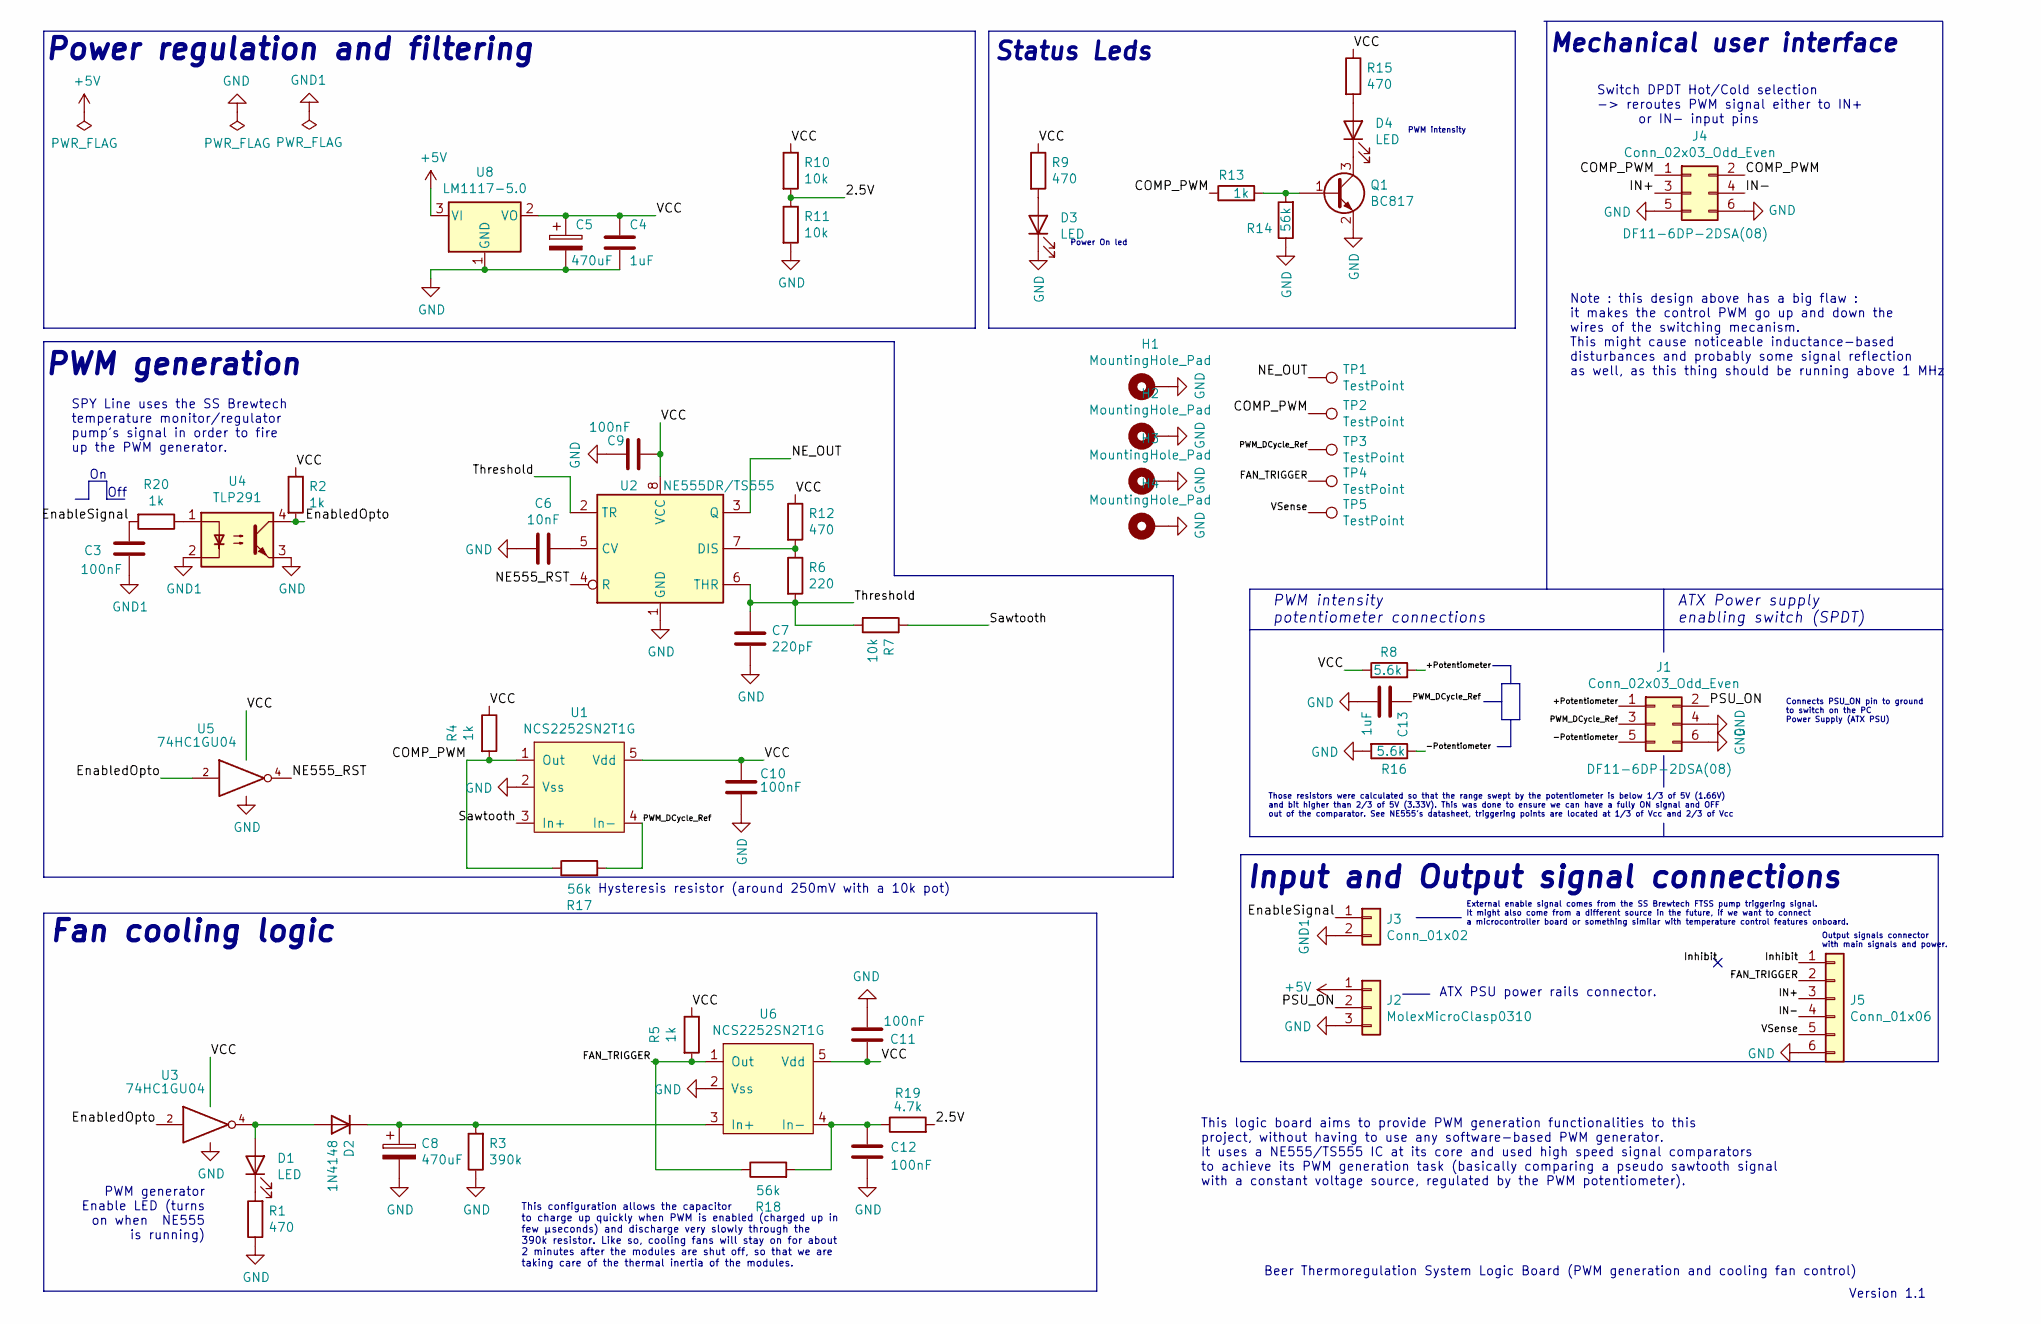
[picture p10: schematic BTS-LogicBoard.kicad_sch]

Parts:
C3, C9, C10, C11, C12: 100nF; C_1206_3216Metric_Pad1.33x1.80mm_HandSolder
C4, C13: 1uF; C_1206_3216Metric_Pad1.33x1.80mm_HandSolder
C5, C8: 470uF; CP_Elec_10x10
C6: 10nF; C_1206_3216Metric_Pad1.33x1.80mm_HandSolder
C7: 220pF; C_1206_3216Metric_Pad1.33x1.80mm_HandSolder
D1, D3, D4: LED; LED_D3.0mm
D2: 1N4148; D_1206_3216Metric_Pad1.42x1.75mm_HandSolder
H1, H2, H3, H4: MountingHole_Pad; MountingHole_3.2mm_M3_DIN965_Pad_TopBottom
J1, J4: Conn_02x03_Odd_Even; Hirose_DF11-6DP-2DSA_2x03_P2.00mm_Vertical; PartNumber DF11-6DP-2DSA(08)
J2: MolexMicroClasp0310; 559350310; PartNumber 55935-0310
J3: Conn_01x02; PinSocket_1x02_P2.54mm_Vertical
J5: Conn_01x06; Molex_MicroLock_1.25_01x06
Q1: BC817; SOT-23
R1, R9, R12, R15: 470; R_1206_3216Metric_Pad1.30x1.75mm_HandSolder
R2, R4, R5, R13, R20: 1k; R_1206_3216Metric_Pad1.30x1.75mm_HandSolder
R3: 390k; R_1206_3216Metric_Pad1.30x1.75mm_HandSolder
R6: 220; R_1206_3216Metric_Pad1.30x1.75mm_HandSolder
R7, R10, R11: 10k; R_1206_3216Metric_Pad1.30x1.75mm_HandSolder
R8, R16: 5.6k; R_1206_3216Metric_Pad1.30x1.75mm_HandSolder
R14, R17, R18: 56k; R_1206_3216Metric_Pad1.30x1.75mm_HandSolder
R19: 4.7k; R_1206_3216Metric_Pad1.30x1.75mm_HandSolder
TP1, TP2, TP3, TP4, TP5: TestPoint; TestPoint_Pad_D2.0mm
U1, U6: NCS2252SN2T1G; SOT-23-5
U2: NE555DR/TS555; SOIC-8_3.9x4.9mm_P1.27mm
U3, U5: 74HC1GU04; SOT-353_SC-70-5
U4: TLP291; SOIC-4_4.55x2.6mm_P1.27mm
U8: LM1117-5.0; SOT-223-3_TabPin2

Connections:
+5V: J2.1, U8.3 (VI)
/2.5V: R10.2, R11.1, R19.2
/+Potentiometer: J1.1, R8.2
/-Potentiometer: J1.5, R16.1
/COMP_PWM: J4.1, J4.2, R4.2, R13.1, R17.1, TP2.1, U1.1 (Out)
/EnableSignal: C3.2, J3.1, R20.2
/EnabledOpto: R2.2, U3.2, U4.4, U5.2
/FAN_TRIGGER: J5.2, R5.2, R18.1, TP4.1, U6.1 (Out)
/IN+: J4.3, J5.3
/IN-: J4.4, J5.4
/NE555_RST: U2.4 (R), U5.4
/NE_OUT: TP1.1, U2.3 (Q)
/PSU_ON: J1.2, J2.2
/PWM_DCycle_Ref: C13.1, J1.3, R17.2, TP3.1, U1.4 (In-)
/Sawtooth: R7.1, U1.3 (In+)
/Threshold: C7.1, R6.2, R7.2, U2.2 (TR), U2.6 (THR)
/VSense: J5.5, TP5.1
GND: C4.2, C5.2, C6.2, C7.2, C8.2, C9.2, C10.2, C11.2, C12.2, C13.2, D3.1 (K), H1.1, H2.1, H3.1, H4.1, J1.4, J1.6, J2.3, J4.5, J4.6, J5.6, Q1.2 (E), R1.1, R3.1, R11.2, R14.1, R16.2, U1.2 (Vss), U2.1 (GND), U3.3 (GND), U4.3, U5.3 (GND), U6.2 (Vss), U8.1 (GND)
GND1: C3.1, J3.2, U4.2
unnamed: C6.1, U2.5 (CV)
unnamed: C8.1, D2.1 (K), R3.2, U6.3 (In+)
unnamed: C12.1, R18.2, R19.1, U6.4 (In-)
unnamed: D1.1 (K), R1.2
unnamed: D1.2 (A), D2.2 (A), U3.4
unnamed: D3.2 (A), R9.2
unnamed: D4.1 (K), Q1.3 (C)
unnamed: D4.2 (A), R15.2
unnamed: Q1.1 (B), R13.2, R14.2
unnamed: R6.1, R12.2, U2.7 (DIS)
unnamed: R20.1, U4.1
VCC: C4.1, C5.1, C9.1, C10.1, C11.1, R2.1, R4.1, R5.1, R8.1, R9.1, R10.1, R12.1, R15.1, U1.5 (Vdd), U2.8 (VCC), U3.5 (VCC), U5.5 (VCC), U6.5 (Vdd), U8.2 (VO)

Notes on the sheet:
Connects PSU_ON pin to ground to switch on the PC Power Supply (ATX PSU)
Output signals connector with main signals and power.
Version 1.1
Fan cooling logic
Off
Mechanical user interface
Power On led
Beer Thermoregulation System Logic Board (PWM generation and cooling fan control)
Hysteresis resistor (around 250mV with a 10k pot)
This logic board aims to provide PWM generation functionalities to this project, without having to use any software-based PWM generator. It uses a NE555/TS555 IC at its core and used high speed signal comparators to achieve its PWM generation task (basically comparing a pseudo sawtooth signal with 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
Those resistors were calculated so that the range swept by the potentiometer is below 1/3 of 5V (1.66V) and bit higher than 2/3 of 5V (3.33V). This was done to ensure we can have a fully ON signal and OFF out of the comparator. See NE555's datasheet, triggering points are located at 1/3 of Vcc and 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
Power regulation and filtering
Input and Output signal connections
Switch DPDT Hot/Cold selection -> reroutes PWM signal either to IN+ or IN- input pins
PWM generator Enable LED (turns on when NE555 is running)
External enable signal comes from the SS Brewtech FTSS pump triggering signal. It might also come from a different source in the future, if we want to connect a microcontroller board or something similar with temperature control features onboard.
This configuration allows the capacitor to charge up quickly when PWM is enabled (charged up in few µseconds) and discharge very slowly through the 390k resistor. Like so, cooling fans will stay on for about 2 minutes after the modules are shut off, so that we are taking care of the thermal inertia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
Note : this design above has a big flaw : it makes the control PWM go up and down the wires of the switching mecanism. This might cause noticeable inductance-based disturbances and probably some signal reflection as well, as this thing should be running above 1 MHz
PWM intensity potentiometer connections
ATX Power supply enabling switch (SPDT)
ATX PSU power rails connector.
SPY Line uses the SS Brewtech temperature monitor/regulator pump's signal in order to fire up the PWM generator.
Status Leds
PWM intensity
PWM generation

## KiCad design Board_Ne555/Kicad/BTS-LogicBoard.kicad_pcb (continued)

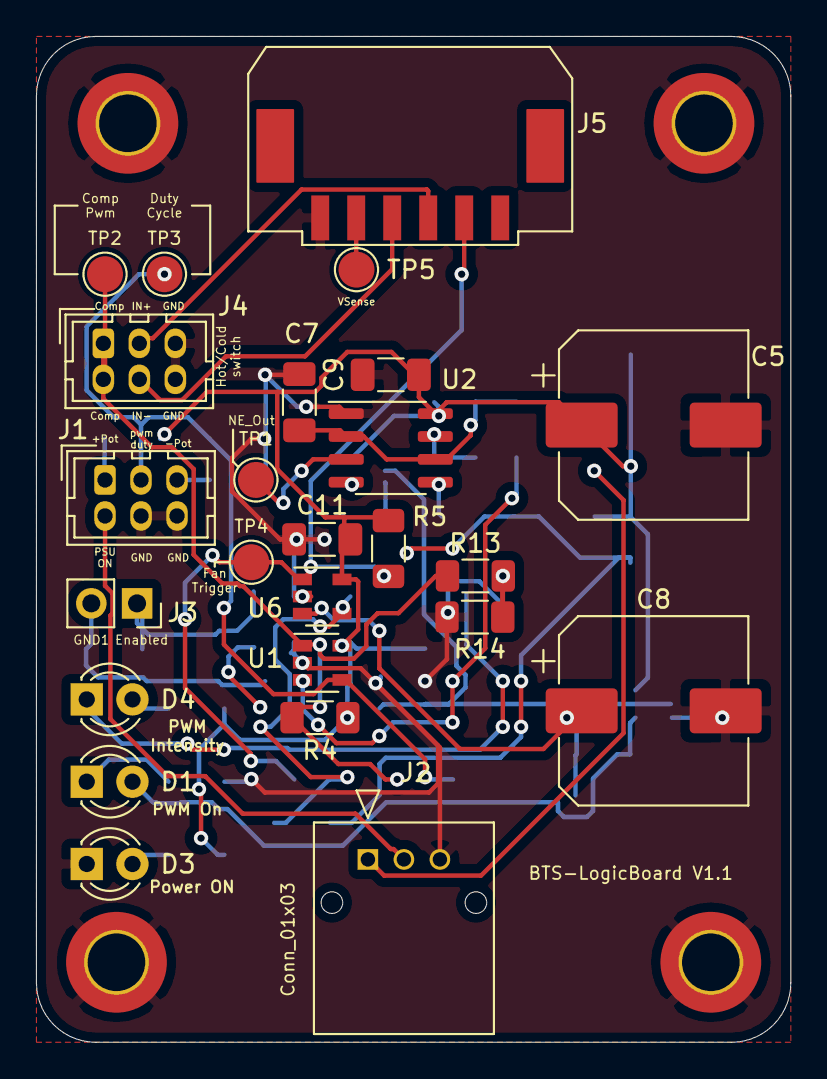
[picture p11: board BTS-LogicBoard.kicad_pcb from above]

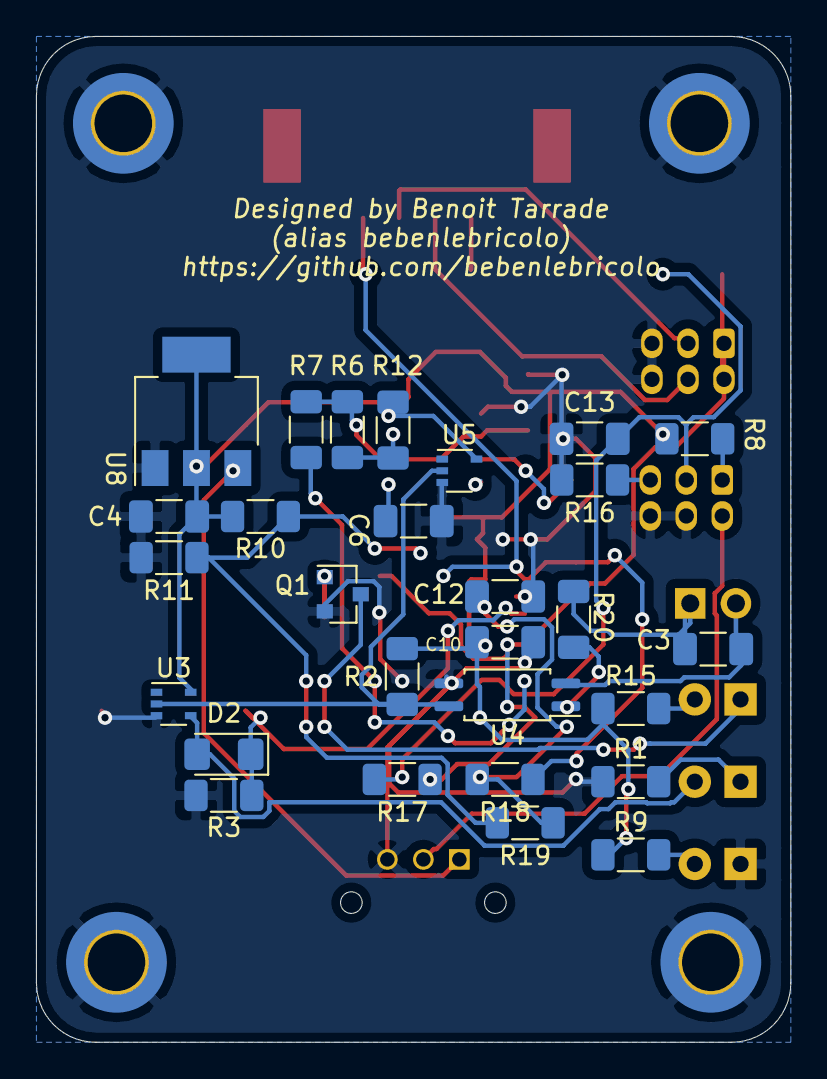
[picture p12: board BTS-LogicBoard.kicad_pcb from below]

Board: 2 copper layers, 41.9 x 55.9 mm, 57 parts (28 on the bottom side), 31 nets.

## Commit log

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2021-10-04 Created Kicad project + gitignore file
    [BTS-LogicBoard.kicad_pcb, BTS-LogicBoard.sch]
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2021-10-04 Started to assign footprints
    [BTS-LogicBoard.sch]
2021-10-04 Added fan triggering simulation
    [BTS-LogicBoard.sch]
2021-10-04 Started footprint placement on board
    [BTS-LogicBoard.kicad_pcb]
2021-10-04 Started routing
    [BTS-LogicBoard.kicad_pcb, BTS-LogicBoard.sch]
2021-10-04 Added NE555 enable override by HIP_DISABLE signal
    [BTS-LogicBoard.kicad_pcb, BTS-LogicBoard.sch]
2021-10-04 Finalized board V1 and exported Gerber files
    [BTS-LogicBoard-B_Cu.gbr, BTS-LogicBoard-B_Mask.gbr, BTS-LogicBoard-B_Paste.gbr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]
2021-10-04 Fan trigger now uses 5V instead of 12v to prevent blowing up fans mosfets
    [BTS-LogicBoard-B_Cu.gbr, BTS-LogicBoard-B_Mask.gbr, BTS-LogicBoard-B_Paste.gbr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]
2021-10-04 Updated Gerbers
    igned-off-by: bebenlebricolo <benoittarrade@hotmail.fr>
    [BTS-LogicBoard-B_Cu.gbr, BTS-LogicBoard-B_Mask.gbr, BTS-LogicBoard-B_Paste.gbr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]
2021-10-04 Created BOM
    [BTS-LogicBoard-BOM.ods]
2021-10-04 Updated silkscreen and Gerbers
    [BTS-LogicBoard-B_Cu.gbr, BTS-LogicBoard-B_Mask.gbr, BTS-LogicBoard-B_Paste.gbr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]
2021-10-04 Updated BOM
    [BTS-LogicBoard-BOM.ods]
2021-10-04 Updated board with optocoupler
    [BTS-LogicBoard-BOM.ods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]
2021-10-04 Fixed unatural DPDT switch mapping
    [BTS-LogicBoard-B_Cu.gbr, BTS-LogicBoard-B_Mask.gbr, BTS-LogicBoard-B_Paste.gbr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]
2021-10-04 Swapped 12Vcc on NE555 outputs and remapped comparators
    [BTS-LogicBoard-B_Cu.gbr, BTS-LogicBoard-B_Mask.gbr, BTS-LogicBoard-B_Paste.gbr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]
2021-10-04 Reworking NCS comparators output interface + led logics
    [BTS-LogicBoard.sch]
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2021-10-05 Updated schematic with proper inverter (not gates) logic layout
    [BTS-LogicBoard.sch]
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2021-10-09 Updated schematic with LEDS and new NE555/TS555 PWM generation circuit
    [BTS-LogicBoard.sch]
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2021-10-09 Restarted layout
    [BTS-LogicBoard.kicad_pcb, BTS-LogicBoard.sch]
2021-10-09 Finalized layout for Version 1.1 (need to work on silkscreen now)
    [BTS-LogicBoard.kicad_pcb, BTS-LogicBoard.sch]
2021-10-10 Finalized board layout with silkscreen
    [BTS-LogicBoard-B_Cu.gbr, BTS-LogicBoard-B_Mask.gbr, BTS-LogicBoard-B_Paste.gbr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]
2021-10-15 Added hysteresis resistor to comparators and reexported gerbers
    [BTS-LogicBoard-B_Cu.gbr, BTS-LogicBoard-B_Mask.gbr, BTS-LogicBoard-B_Paste.gbr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]
2021-10-15 Forgot to add another hysteresis resistor : done
    [BTS-LogicBoard-B_Cu.gbr, BTS-LogicBoard-B_Mask.gbr, BTS-LogicBoard-B_Paste.gbr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]
2021-10-29 Added prototype v1.1 bom
    [BTS-LogicBoard-BOM-prototype-1.0.ods, BTS-LogicBoard-BOM-prototype-1.1.ods]
2021-10-29 Annotated schematic
    [BTS-LogicBoard-BOM.ods, BTS-LogicBoard.sch]
2021-11-09 Added some Simulations to test discrete h bridge driver implementations
    [BTS-LogicBoard-BOM-prototype-1.1.ods]
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2022-01-03 Moved Ne555 based board design elements to the right folder
    [BTS-LogicBoard-BOM-prototype-1.0.ods, BTS-LogicBoard-BOM-prototype-1.1.ods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]
2022-01-03 Added pin compatibilities calc file to compare two avr mcus
    [PinCompatibilities.ods]
2022-01-03 Started LogicBoard desing based on avr mcus
    [LogicBoard_Avr.kicad_pcb, LogicBoard_Avr.kicad_sch]
2022-01-03 Added the Mechanical user interface hierarchical sheet and started schematics
    [LogicBoard_Avr.kicad_sch, MechanicalUserInterface.kicad_sch]
2022-01-03 Designed basic layout for the mechanical user interface
    [LogicBoard_Avr.kicad_sch, MechanicalUserInterface.kicad_sch]
2022-01-03 Added several other schematic sheets
    [LogicBoard_Avr.kicad_sch, MechanicalUserInterface.kicad_sch, PowerBoardLink.kicad_sch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]
2022-01-04 Added several external connections and reworked leds and output signals
    [ExternalInterface.kicad_sch, LogicBoard_Avr.kicad_sch, MechanicalUserInterface.kicad_sch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]
2022-01-04 Updated pin configurations in PinCompatibilities.ods
    [PinCompatibilities.ods]
2022-01-04 Fixed misorganised pins and updated pin mapping table
    [ExternalInterface.kicad_sch, LogicBoard_Avr.kicad_sch, PinCompatibilities.ods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]
2022-01-05 Started routing all traces
    [ExternalInterface.kicad_sch, LogicBoard_Avr.kicad_pcb, LogicBoard_Avr.kicad_sch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]
2022-01-05 Removed all microvias (unsupported by JLCPCB)
    [LogicBoard_Avr.kicad_pcb, LogicBoard_Avr.kicad_sch]
2022-01-06 Rerouted parts of the board and improved zones
    [LogicBoard_Avr.kicad_pcb]
2022-01-06 Updated VCC and 3.3V zones
    [LogicBoard_Avr.kicad_pcb]
2022-01-06 Finalised routing
    [LogicBoard_Avr.kicad_pcb, LogicBoard_Avr.kicad_sch, PowerBoardLink.kicad_sch]
2022-01-06 Cleaned last remaining track bits
    [LogicBoard_Avr.kicad_pcb]
2022-01-06 Same using the automatic cleanup tracks and via tool
    [LogicBoard_Avr.kicad_pcb]
2022-01-06 Fixed silkscreen and added PWM signal test points
    [LogicBoard_Avr.kicad_pcb, LogicBoard_Avr.kicad_sch, PowerBoardLink.kicad_sch]
2022-01-07 Tweaked top silkscreen to embed useful information
    [LogicBoard_Avr.kicad_pcb, LogicBoard_Avr.kicad_sch, PowerRegulation.kicad_sch]
2022-01-07 Finalised routing and finalised silkscreen
    [LogicBoard_Avr.kicad_pcb, LogicBoard_Avr.kicad_sch, MechanicalUserInterface.kicad_sch]
2022-01-07 Backed up modifications on schematic as well
    [LogicBoard_Avr.kicad_sch, MechanicalUserInterface.kicad_sch]
2022-01-14 Replaced TLV1117-3.3 by NCP630SN330 and polished a bit zoning
    [LogicBoard_Avr.kicad_pcb, LogicBoard_Avr.kicad_sch, PowerRegulation.kicad_sch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]
2022-01-15 Removed unused pads from vias in order to improve polygons
    [LogicBoard_Avr.kicad_pcb]
2022-01-19 Added BTS logos and updated silkscreen
    [LogicBoard_Avr.kicad_pcb]
2022-01-20 Generated Gerbers and BOM files
    [BOM_LogicBoard_Avr_Rev_0.3.0.ods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]
2022-01-20 Moved Gerbers around and updated 3d model of optocoupler
    [LogicBoard_Avr-B_Cu.gbr, LogicBoard_Avr-B_Mask.gbr, LogicBoard_Avr-B_Paste.gbr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]
2022-01-24 Updated ferrite bead footprint
    [BOM_LogicBoard_Avr_Rev_0.3.0.ods, LogicBoard_Avr.kicad_pcb, LogicBoard_Avr.kicad_sch]
2022-02-23 Updated board with external clock for both mcus + thermal reliefs update
    [LogicBoard_Avr.kicad_pcb, LogicBoard_Avr.kicad_sch, clocking.kicad_sch]

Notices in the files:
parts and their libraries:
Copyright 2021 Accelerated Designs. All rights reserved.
